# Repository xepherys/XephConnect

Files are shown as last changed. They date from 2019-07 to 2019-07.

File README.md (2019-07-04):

# XephConnect
Daughter Board / Breakout Board for moving Duet connections to the tool.

This PCB design is being created for the RailCore II to move carriage-based connections (extruder steppers, thermistor, heater, Y-stop) to the tool using a single wire harness.

The idea for this started with my desire to create a tool carriage for the M3D QuadFusion, which has four (4) extruder steppers, but being able to run a single connector up to the tool that can swap between the QuadFusion and the E3D standard hotends.

In current iterations, the design calls for a TE 32-pin connector.  See PARTLIST.txt in the individual version folder for information on the components required.  See VERNOTES.txt for information and notes on each version.

v0.1 was the original design.  I hadn't designed a PCB in quite some time, and used auto-router. Not the greatest plan.  It's functional (it's on my RailCore II 300ZL currently, as of 7/4/19), but it has some issues with noise from the steppers interfering with the z-probe, and a few issues with hole spacing (one of the screws doesn't play nicely with one of the Molex headers).

v0.6, as of this update (7/4/19) is being manufactured as a prototype.  I should be testing it as soon as it arrives.  It requires different wiring of the main wire harness, but also includes wiring for the heater cartridge.

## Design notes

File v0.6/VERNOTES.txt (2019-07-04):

Version Notes (XephConnect v0.6):

Designed to provide the following connectivity at the tool from the Duet Wifi + Duex5:

  * Stepper motors (4x) [4-wire] - conceptually to drive the four extruders in the M3D QuadFusion, but could theoretically connect any four steppers.
  * Hotend thermistor [2-wire]
  * Hotend heater cartridge [2-wire] {see note on WIRING below}
  * Hotend/Heatsink fan [2-wire, always on] {see note on FANS below}
  * Part cooling fan [2-wire, PWM] {see note on FANS below}
  * X-stop [2-wire]
  * Y-stop [2-wire]
  * Z-probe [4/5-wire] - ONLY USE ONE OF THESE.  The 4-wire is for standard z-probes (currently tested with the Precision Piezo Orion), and the 5-wire should work with the BL-touch, though this is untested.

FANS:
-----

An additional feature that is being worked on for the board is to bring up 5v, 12v, and 24v power connections and allow both fans to have their voltage selected via jumper. On this version it does work, though the 24v and VOUT pads are larger than necessary, and the silkscreen gets hidden a bit by the jumper headers.  I'm currently running my heatsink fan, always on, at 12v and my parts cooling fan, PWM, at 24v.  The +12v draw comes from the static 12v header on the Duex5.  The +24v can come from any 24v source (generally any PWM power pin on either board).  The +5v isn't hooked up in my current testing.

POWER:
------

While the bandwidth on the wiring harness allows for FAN1- and FAN2- PWM connections to also be run, I don't currently have them wired or have headers on the board for them.

+5v, +12v, and +24v as well as GND are common rails/planes.  Take care having too many devices on a single power setting to prevent overdraw of power from a single pin on the Duet/Duex.  Fans typically use very little power, but LEDs can consume much more.  GND is dual-wired back to ground to the Duet board (pin 5 from the harness) and Duex board (ping 30 from the harness).  Given that the two boards _should_ be wired in such a way that they also share a ground (one is pigtailed to the other), this allows a common ground voltage throughout the system.

WIRING:
-------

Just as the board traces are varying widths for different paths, the wires for your harness also have different requirements.  22AWG (and even 24AWG) can be used for signals (THERM1, Z_IN, Z_MOD, +3.3v for Z_PROBE, X_STOP, Y_STOP). 22AWG (but not 24AWG) can be used for the steppers, +5v, +12v, and +24v leads, FAN0-.  20AWG is recommended for GND and the heater cartridge.

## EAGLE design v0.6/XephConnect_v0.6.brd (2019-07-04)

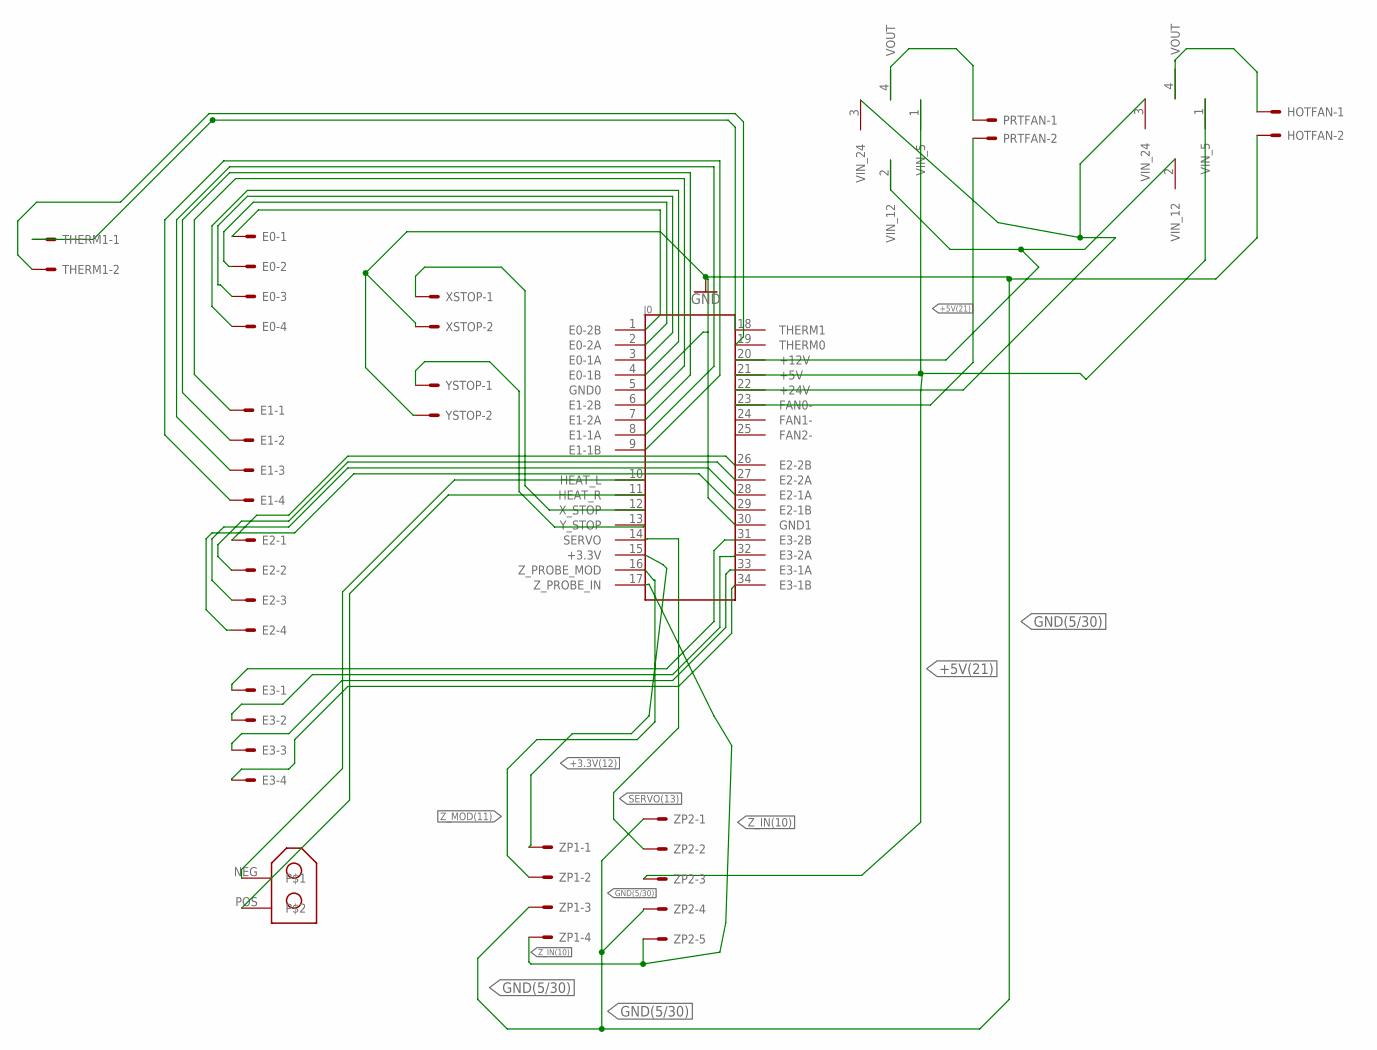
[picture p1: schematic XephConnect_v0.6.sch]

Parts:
E0, E1, E2, E3: 22-27-2041-04; 6410-04
HOTFAN: 22-27-2021-02; 6410-02
J0: 6437288-1-V2; TE_6437288-1
PRTFAN: 22-27-2021-02; 6410-02
THERM1: 22-27-2021-02; 6410-02
U$1, U$2: CONN_03+01(T)(SM); 1X03X01(SM)
U$3: XT30; XT30-90
XSTOP: 22-27-2021-02; 6410-02
YSTOP: 22-27-2021-02; 6410-02
ZP1: 22-27-2041-04; 6410-04
ZP2: 22-27-2051-05; 6410-05

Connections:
+3.3V(12): J0.15 (+3.3V), ZP1.1
+5V(21): J0.21 (+5V), U$1.1 (VIN_5), U$2.1 (VIN_5), ZP2.3
+12V(20): J0.20 (+12V), U$1.2 (VIN_12), U$2.2 (VIN_12)
+24V(22): J0.22 (+24V), U$1.3 (VIN_24), U$2.3 (VIN_24)
E0-1A: E0.3, J0.3 (E0-1A)
E0-1B: E0.4, J0.4 (E0-1B)
E0-2A: E0.2, J0.2 (E0-2A)
E0-2B: E0.1, J0.1 (E0-2B)
E1-1A: E1.3, J0.8 (E1-1A)
E1-1B: E1.4, J0.9 (E1-1B)
E1-2A: E1.2, J0.7 (E1-2A)
E1-2B: E1.1, J0.6 (E1-2B)
E2-1A: E2.3, J0.28 (E2-1A)
E2-1B: E2.4, J0.29 (E2-1B)
E2-2A: E2.2, J0.27 (E2-2A)
E2-2B: E2.1, J0.26 (E2-2B)
E3-1A: E3.3, J0.33 (E3-1A)
E3-1B: E3.4, J0.34 (E3-1B)
E3-2A: E3.2, J0.32 (E3-2A)
E3-2B: E3.1, J0.31 (E3-2B)
FAN0-(23): J0.23 (FAN0-), PRTFAN.2
FAN1-: J0.24 (FAN1-)
FAN2-: J0.25 (FAN2-)
GND(5/30): HOTFAN.2, J0.5 (GND0), J0.30 (GND1), XSTOP.2, YSTOP.2, ZP1.3, ZP2.1, ZP2.4
HEAT0: J0.10 (HEAT_L), U$3.NEG
HEAT1: J0.11 (HEAT_R), U$3.POS
unnamed: HOTFAN.1, U$2.4 (VOUT)
unnamed: PRTFAN.1, U$1.4 (VOUT)
SERVO(13): J0.14 (SERVO), ZP2.2
THERM0: J0.18 (THERM1), THERM1.1
THERM1: J0.19 (THERM0), THERM1.2
X_STOP: J0.12 (X_STOP), XSTOP.1
Y_STOP: J0.13 (Y_STOP), YSTOP.1
Z_IN(10): J0.17 (Z_PROBE_IN), ZP1.4, ZP2.5
Z_MOD(11): J0.16 (Z_PROBE_MOD), ZP1.2

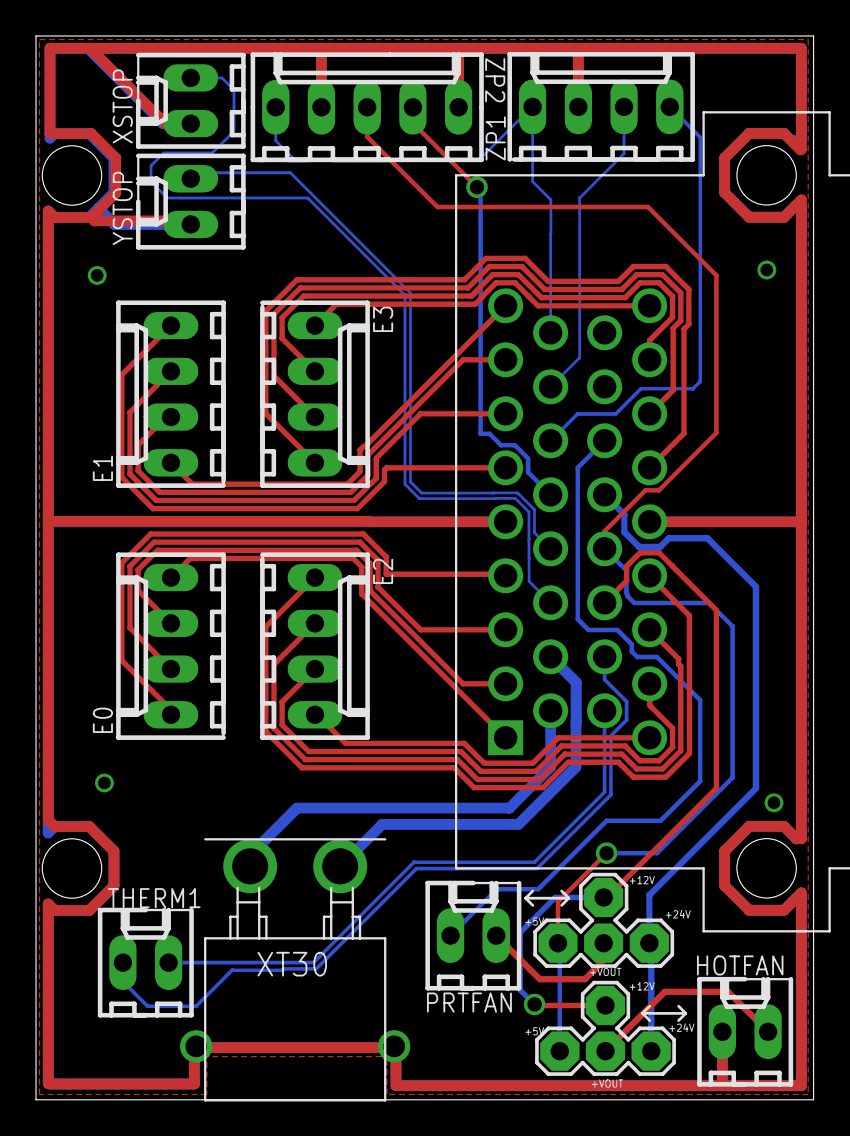
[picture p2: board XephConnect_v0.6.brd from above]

Board: 2 copper layers, 43.2 x 59.1 mm, 15 parts (0 on the bottom side), 33 nets.

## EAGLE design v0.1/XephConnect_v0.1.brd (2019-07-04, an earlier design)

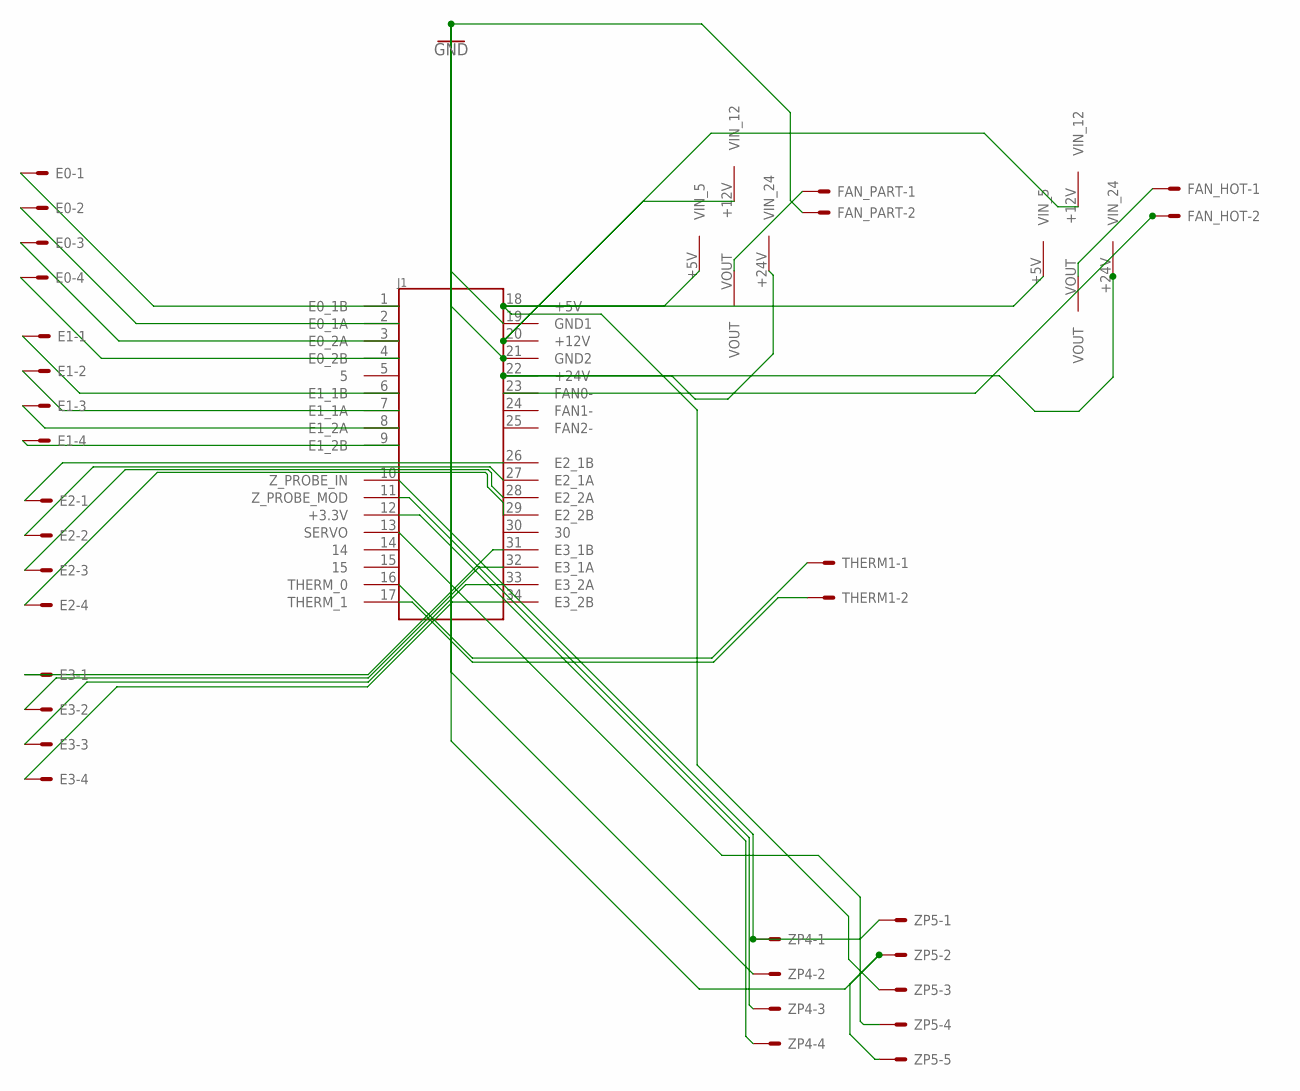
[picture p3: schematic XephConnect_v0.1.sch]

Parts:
E0, E1, E2, E3: 22-27-2041-04; 6410-04
FAN_HOT: 22-27-2021-02; 6410-02
FAN_PART: 22-27-2021-02; 6410-02
J1: 6437288-1; TE_6437288-1
THERM1: 22-27-2021-02; 6410-02
U$1, U$2: CONN_03+01(T); 1X03X01
ZP4: 22-27-2041-04; 6410-04
ZP5: 22-27-2051-05; 6410-05

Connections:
FAN1-: J1.24 (FAN1-)
FAN2-: J1.25 (FAN2-)
GND: FAN_PART.2, J1.19 (GND1), J1.21 (GND2), ZP4.2, ZP5.2, ZP5.5
unnamed: E0.1, J1.1 (E0_1B)
unnamed: E0.2, J1.2 (E0_1A)
unnamed: E0.3, J1.3 (E0_2A)
unnamed: E0.4, J1.4 (E0_2B)
unnamed: J1.10 (Z_PROBE_IN), ZP4.1, ZP5.1
unnamed: E1.1, J1.6 (E1_1B)
unnamed: E1.2, J1.7 (E1_1A)
unnamed: E1.3, J1.8 (E1_2A)
unnamed: E1.4, J1.9 (E1_2B)
unnamed: E2.1, J1.26 (E2_1B)
unnamed: E2.2, J1.27 (E2_1A)
unnamed: E2.3, J1.28 (E2_2A)
unnamed: E2.4, J1.29 (E2_2B)
unnamed: E3.1, J1.31 (E3_1B)
unnamed: E3.2, J1.32 (E3_1A)
unnamed: E3.3, J1.33 (E3_2A)
unnamed: E3.4, J1.34 (E3_2B)
unnamed: J1.16 (THERM_0), THERM1.1
unnamed: J1.17 (THERM_1), THERM1.2
unnamed: J1.18 (+5V), U$1.+5V (VIN_5), U$2.+5V (VIN_5), ZP5.3
unnamed: J1.20 (+12V), U$1.+12V (VIN_12), U$2.+12V (VIN_12)
unnamed: FAN_HOT.2, J1.23 (FAN0-)
unnamed: J1.22 (+24V), U$1.+24V (VIN_24), U$2.+24V (VIN_24)
unnamed: FAN_PART.1, U$1.VOUT
unnamed: FAN_HOT.1, U$2.VOUT
unnamed: J1.11 (Z_PROBE_MOD), ZP4.3
unnamed: J1.12 (+3.3V), ZP4.4
unnamed: J1.13 (SERVO), ZP5.4

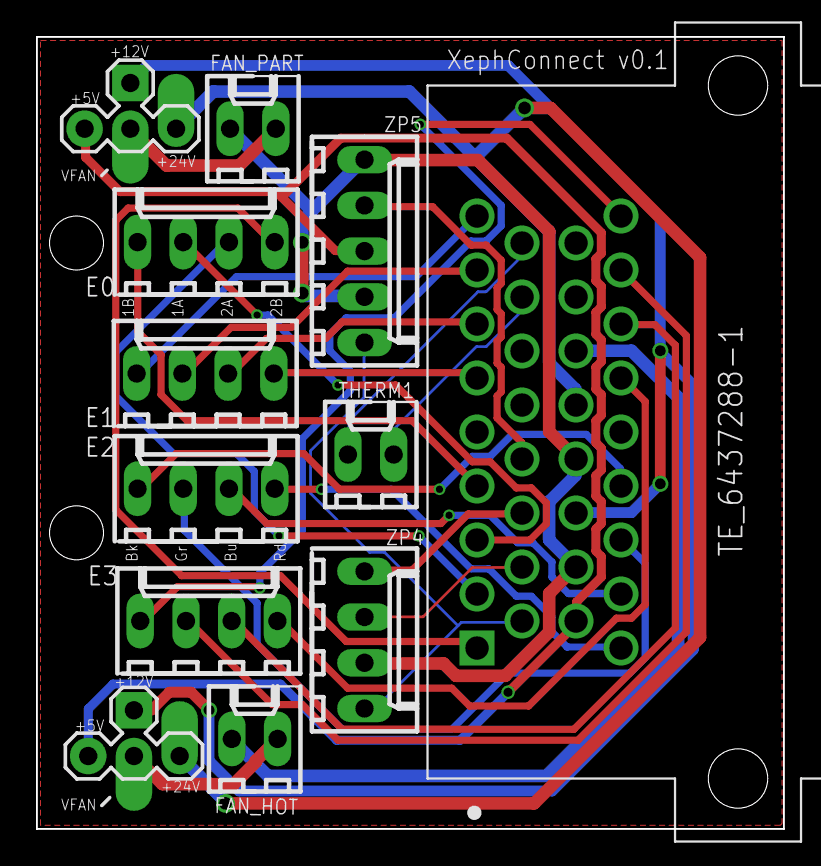
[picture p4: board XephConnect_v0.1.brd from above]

Board: 2 copper layers, 41.5 x 44.0 mm, 12 parts (0 on the bottom side), 29 nets.

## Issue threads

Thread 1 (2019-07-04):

v0.1 - extruder being energized causes analog Orion to have high or low standing readings

xepherys, 2019-07-04:
Extruder being energized causes analog Orion to have high or low standing readings, a dip or rise of about ±50. Moving the Orion wiring back to the Duet and leaving the board allows it to function as expected.  Disabling the extruder stepper immediately restores it to its normal standing value.

xepherys, 2019-07-04:
I believe this may have to do with the auto-routing of traces on the v0.1.  Later revisions are manually routed, keeping the stepper traces away from signal traces as much as possible, and when signal needs to cross stepper traces, it does so perpendicularly in as short an area as possible.

Waiting for v0.6 prototype to see if this resolves it.

xepherys, 2019-08-16:
v0.6 is in testing now and moves stepper wiring and traces away from signal wiring and traces.

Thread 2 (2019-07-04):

v0.1 - Orion sometimes triggers more harshly, especially after X/Y movement

xepherys, 2019-07-04:
Orion sometimes triggers more harshly, especially after X/Y movement, though not always.  Shutting the power off entirely and bringing it back up does seem to resolve the issue 100% of the time.  Further investigation needed.  Will continue looking into it and retest with v0.6 when it arrives as well.

xepherys, 2019-08-16:
Determined it was actually caused by noise from the extruded stepper after extruded operations. Either direction changed the resting point for the Orion analog board +/- as much as 40.

v0.6 is in testing now and moves stepper wiring and traces away from signal wiring and traces.

xepherys, 2019-08-16:
See bug #4.

Closed 2019-08-16.

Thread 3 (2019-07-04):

v0.1 - should run wires in harness for heater cartridge

xepherys, 2019-07-04:
Want to add heater cartridge wiring to harness - currently separate.

xepherys, 2019-07-04:
v0.6 includes spot for XT30 header (personal preference for heater cartridge). Expecting to use 20AWG for these two wires.

Closed 2019-07-04.

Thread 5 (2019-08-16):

Find smaller connector option

xepherys, 2019-08-16:
The current TE connector is great due to its high pin count and extreme ease of inserting pins. Some connectors were very difficult to insert pins without special (expensive) tooling.

However, a smaller connector would be ideal.

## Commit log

2019-07-04 Upload of v0.1 and v0.6 designs
    Eagle .brd/.sch uploads and CAM outputs (Gerber + Drill) for v0.1 and v0.6 of the XephConnect board.
    [XephConnect_v0.1.brd, XephConnect_v0.1.sch, XephConnect_v0.6.brd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]
2019-07-04 Update v0.1 to have ground plane
    [drills.xln, gerber_job.gbrjob]

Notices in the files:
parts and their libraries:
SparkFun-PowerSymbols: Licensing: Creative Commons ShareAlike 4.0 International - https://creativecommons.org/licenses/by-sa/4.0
